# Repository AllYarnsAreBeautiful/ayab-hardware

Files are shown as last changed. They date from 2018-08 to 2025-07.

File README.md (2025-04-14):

# AYAB Hardware
This is the respository for the open-source first-party hardware that interfaces with the AYAB desktop software. It contains design files, production files, and assembly documentation, sorted by hardware generation.

The AYAB project started with the original AYAB Shield, which mounts to an Arduino Uno. The shield does not fit inside the machine and it must remain open while installed. These are often sold in kits and require assembly by the user.\
This design was later incorporated into a replacement PCB to be installed into the knitting machine, called the AYAB-Interface, and was designed and produced by Evil Mad Scientist Labs (EMSL).\
In anticipation of the new generation of AYAB software with the launch of v1.0, we have also started design on a new generation of hardware with a custom, fully integrated ESP32 microcontroller. AYAB-ESP32 supports KH 270, 900, 910, 930, 940, 950, 965, and CK-35, which would replace the internal motherboard of the knitting machine (in an easily reversible way) and allow for wireless pattern upload and operation from various mobile devices.

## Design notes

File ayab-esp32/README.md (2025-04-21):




# AYAB-ESP32
These are the design files for the latest generation of AYAB hardware, a new, next controller for knitting machines.\
It currently has compatibility with the Brother KH 900, 910, 930, 940, 950, 965, with support planned for CK-35 and KH-270.\
Based on the ESP32, many new features have been implemented:\

* Supports all carriages (K, L, and G)
* Can be powered from internal Brother power supply, or 9-12V DC barrel jack of any polarity.
* PC connection via USB-C, with future web-app planned for "wireless" use.
* Qwiic I2C connector available for user expansion or accessories (color changer, motorized carriage, etc)
* 8 User-accessible GPIO brought out on 2.54mm headers.
* 1 User-programmable button.
* Hackable - access to the solenoid control bus from outside devices for direct control of the machine.
* Friendly design for assembly. Single-sided PCB with minimum package size of 0603 and optimized BOM.
* OSHW certified design!

The project was designed using KiCad 8. All symbols, footprints, and models are self contained to this repository so no additional files are required in order to view or modify the design.

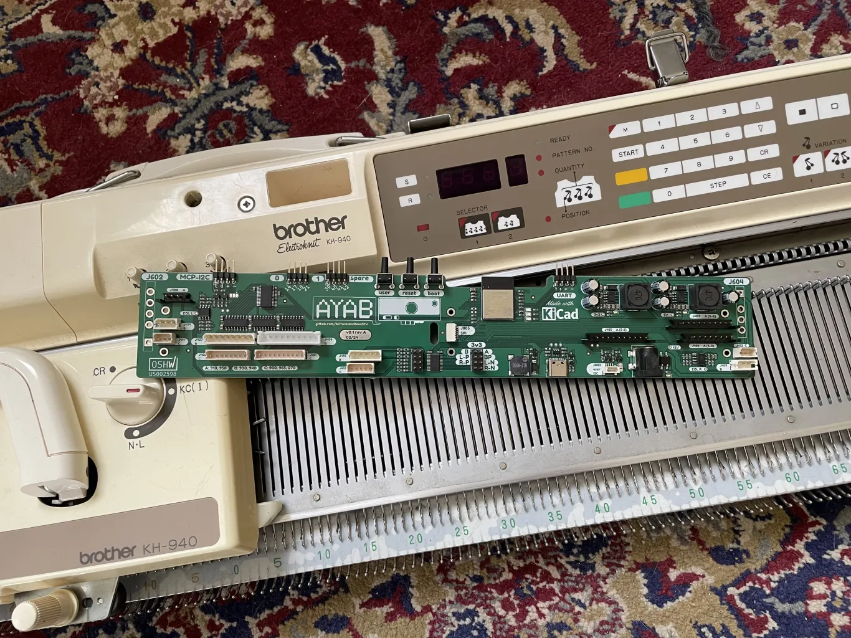
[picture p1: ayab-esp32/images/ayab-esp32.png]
Prototype hardware assembly

Live Render

Questions? Comments? Great ideas? Talk with us in [#hardware-development on Discord](https://discord.gg/A8KE3jcCn2)!

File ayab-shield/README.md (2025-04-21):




# AYAB Shield
This is the original design for the AYAB hardware. It is a board in a shield form factor intended to be used with Arduino Uno type development boards. It should be compatible with Uno R2, R3, and R4. 
This shield can be built in a variety of configurations that allow for compatibility with Brother KH 270, 900, 910, 930, 940, 950, 965.

The files required to order/build the board can be found in the Releases on the sidebar, but you can also find workflow artifacts for unvalidated hardware based on the state of the repo.

The project was designed using KiCad 9. All symbols, footprints, and 3D models are self-contained to the repository.

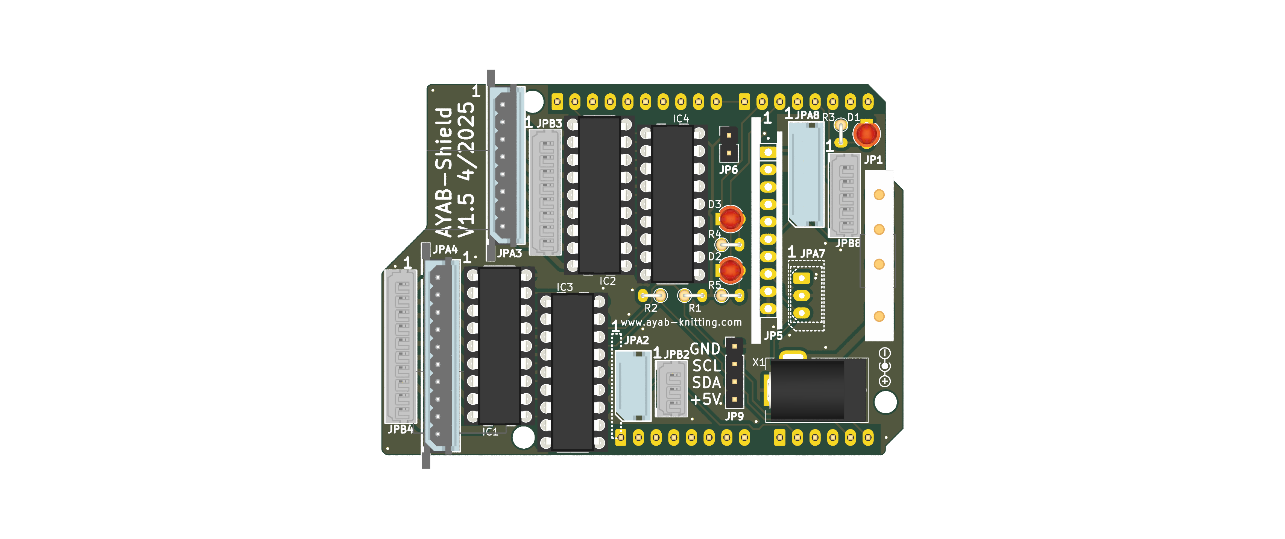
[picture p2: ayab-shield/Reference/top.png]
Live Render


Questions? Comments? Great ideas? Talk with us in [#hardware-development on Discord](https://discord.gg/A8KE3jcCn2)!

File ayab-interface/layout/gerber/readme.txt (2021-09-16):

AYAB-EMS Interface Board - Rev F
Designed by Evil Mad Scientist Laboratories
in cooperation with ayab-knitting.com

An open source hardware+software project. :)

This directory contains the following files:
 
ayab_rs.top.gbr	   			- Top copper artwork
ayab_rs.topmask.gbr 			- Top soldermask
ayab_rs.topsilk.gbr			- Top Silkscreen 

ayab_rs.bottom.gbr	 		- bottom copper artwork
ayab_rs.bottommask.gbr		  	- bottom soldermask
ayab_rs.bottomsilk.gbr			- Bottom Silkscreen

ayab_rs.plated-drill.cnc      		- NC drill file (For plated holes)
ayab_rs.unplated-drill.cnc    		- NC drill file (for unplated holes)

ayab_rs.DrillDrawing.gbr   	 	- drill Drawing with outline 
ayab_rs.outline.gbr			- Outline drawing

ayab_rs.toppaste.gbr    	 	- Solder paste file (top)

The PCB specifications are as follows:

All specifications given in INCHES or MILS.
Board size (max): 11.000 x 1.900 INCHES   (279.4 mm x 48.3 mm) 
Material: FR4
Thickness: 0.062" (1.6 mm) nominal
Layers: 2
Copper weight: 1 oz.

Individual routing according to outline on ayab_rs.outline.gbr layer.

Min Trace/Space: 8 mil
Min. Annular Ring: 12 mil

The following additional specifications are default for this board:

Finish: Pb-Free HASL, RoHS Compliant
Soldermask: BLACK LPI, both sides
Silkscreen Legend: WHITE, both sides.

UL Compliant with mark.  Add UL mark to BOTTOM SILKSCREEN.

NO FACTORY MARKS ALLOWED ON TOP SIDE OF PCB
FACTORY MARKINGS MAY BE APPLIED TO BOTTOM SIDE OF PCB (IN SILK) IF NECESSARY.

RoHS Compliant fabrication
Full electrical test of printed circuit boards is required.

NO CHANGE to any copper without prior approval.

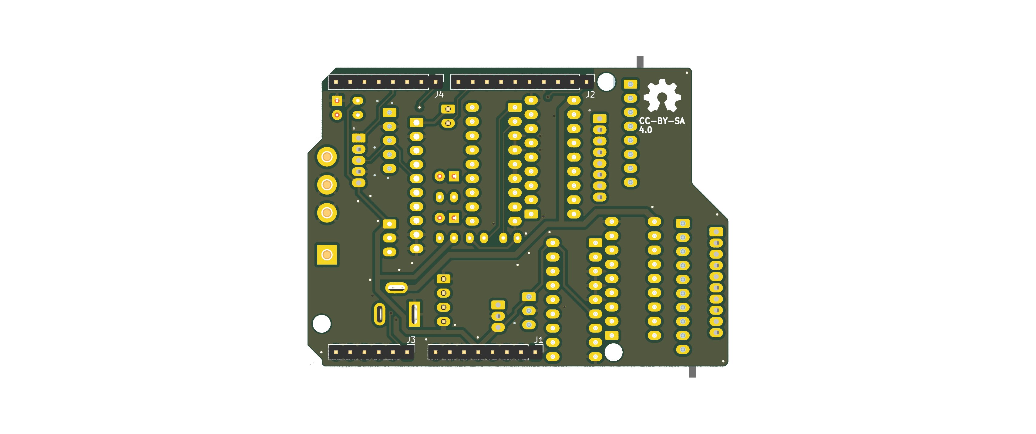
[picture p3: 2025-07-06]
ayab-shield/Reference/bottom.png

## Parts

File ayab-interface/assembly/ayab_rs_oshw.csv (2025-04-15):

Line | QTY | Reference | Type | Value | Footprint | Pin Count | Side | Manf | Manf PN | Alt. Manf | Alt Manf PN | DIGI-KEY # | Mouser # | Fabrication note
1 | 1 | - | PCB | AYAB-EMS-1 Circuit Board |  |  |  |  | 60-0043/E
2 | 1 | U1 | Microcontroller | Adafruit Metro Mini |  | 28 | BOT | Adafruit | 2590 |  |  | 1528-1374-ND | 485-2590 | DO NOT POPULATE. Mask holes if wave soldered
3 | 2 | U1 | Header | Header, 0.1", 14-pin, male-male short | PTH | 14 | BOT | 4UCon | 17168
4 | 1 | S1 | Switch | Tactile button switch | SMT Switch | 4 | TOP | TE Connectivity | FSM4JSMATR |  |  | 450-1129-ND | 506-FSM4JSMATR
5 | 1 | L1 | Buzzer | BUZZER MAGN 5V 2.4KHZ PCB | PTH | 2 | TOP | PUI | AT-1224-TWT-5V-2-R | Soberton | WT-1205 | 668-1470-ND | 665-AT1224TWT5V2R
6 | 4 | C1,C4,C5,C6 | Capacitor | 1 uF Ceramic 1206 | 1206 | 2 | TOP | Kemet | C1206C105M3RACTU |  |  | 399-8148-1-ND | 80-C1206C105M3R
7 | 1 | C2 | Capacitor | 0.1 uF Ceramic 0603 | 603 | 2 | TOP | Kemet | C0603C104K3RACTU |  |  | C0603C104K3RACTU | 80-C0603C104K3R
8 | 1 | C3 | Capacitor | 22 uF 20 V tantalum, Case B | SMT Cap. | 2 | TOP | AVX | AVX_TAJB226K020RNJ | AVX | AVX_TAJB226M020RNJ | 478-1683-1-ND | 581-TAJB226K020R
9 | 1 | D1 | Diode | DIODE SCHOTTKY 40V 2A | DO214AA | 2 | TOP | Micro Commercial | SK24-TP |  |  | SK24-TPCT-ND | 833-SK24-TP
10 | 4 | D2, D3, D5, D6 | LED | SMT RA, blue, 90 mCd min. | 805 | 2 | TOP | Lite-On | LTST-S220TBKT | Kingbright | APA2106QBC/D | 160-2032-1-ND | 859-LTST-S220TBKT
11 | 3 | R1, R7, R8 | Resistor | 5k, 5%, 1/8 W | 805 | 2 | TOP | Stackpole | RNCP0805FTD4K99 | Bourns | CR0805-FX-4991ELF | RNCP0805FTD4K99CT-ND | 652-CR0805FX-4991ELF
12 | 4 | R2, R4, R5, R6 | Resistor | 62, 1/4W or higher | 805 | 2 | TOP | Rohm | ESR10EZPJ620 |  |  | RHM62KCT-ND | 755-ESR10EZPJ620
13 | 1 | R3 | Resistor | 330, 5%, 1/4W | 805 | 2 | TOP | Rohm | ESR10EZPJ331 |  |  | ESR10EZPJ331 | 755-ESR10EZPJ331
14 | 4 | RN1,RN2,RN3,RN4 | Resistor array | 1k, 5%, 4 X Isolated array | 1206 | 8 | TOP | Yageo | YC164-JR-071KL | Bourns | CAT16-102J4GLF | YC164J-1.0KCT-ND | 652-CAT16-102J4GLF
15 | 1 | Q1 | Transistor | NPN 40V 0.2A | SOT-23-3 | 2 | TOP | ON Semi | MMBT3904LT1G |  |  | MMBT3904LT1GOSCT-ND | 863-MMBT3904LT1G
16 | 2 | U2,U3 | IC | PCF8574, I2C IO Expander | 16-SOIC | 16 | TOP | TI | PCF8574DWR | NXP | PCF8574T/3,512 | 296-13108-1-ND | 595-PCF8574DWR
17 | 2 | U4, U5 | IC | ULN2803A, Transistor array | SO-18W | 18 | TOP | TI | ULN2803ADWR | Toshiba | ULN2803AFWG | 296-15777-1-ND | 595-ULN2803ADWR
18 | 1 | J5 | Jack | Power Jack, 2.1x5.1 mm, rated for 2A DC | PTH | 3 | BOT | CUI | CP-002AH-ND | CUI | PJ-002AH | CP-002AH-ND | 490-PJ-002AH | Bottom side of PCB
19 | 2 | J2B, J6B | Molex Jack (2.5mm) | Molex 5267 Series, 3 position Male | PTH | 3 | TOP | Molex | 99-99-0987 | 4UCON | 1678 | WM2889-ND | 538-99-99-0987 | Orientation of connectors is critical
20 | 1 | J3B | Molex Jack (2.5mm) | Molex 5267 Series, 5 position Male | PTH | 5 | TOP | Molex | 99-99-0989 | 4UCON | 1680 | WM2891-ND | 538-99-99-0989 | Orientation of connectors is critical
21 | 1 | J4B | Molex Jack (2.5mm) | Molex 5267 Series, 8 position Male | PTH | 8 | TOP | Molex | 99-99-0992 | 4UCON | 1683 | 0099990992-ND | 538-99-99-0992 | Orientation of connectors is critical
22 | 1 | J5B | Molex Jack (2.5mm) | Molex 5267 Series, 10 position Male | PTH | 10 | TOP | Molex | 99-99-0994 | 4UCON | 1685 | 0099990994-Nd | 538-99-99-0994 | Orientation of connectors is critical
23 | 2 | J2C,J6C | Molex Jack (2mm) | Molex 53014 series, 3 position male | PTH | 3 | TOP | Molex | 53014-0310 | Molex | 53253-0870 | WM18967-ND | 538-53253-0870 | Orientation of connectors is critical
24 | 1 | J3C | Molex Jack (2mm) | Molex 53014 series, 5 position male | PTH | 5 | TOP | Molex | 53014-0510 | Molex | 53253-1070 | WM18968-ND | 538-53253-1070 | DO NOT POPULATE. Mask holes if wave soldered
25 | 1 | J4C | Molex Jack (2mm) | Molex 53014 series, 8 position male | PTH | 8 | TOP | Molex | 53014-0810 | Molex | 53253-0370 | WM18971-ND | 538-53253-0370 | DO NOT POPULATE. Mask holes if wave soldered
26 | 1 | J5C | Molex Jack (2mm) | Molex 53014 series, 10 position male | PTH | 10 | TOP | Molex | 53014-1010 | Molex | 53253-0570 | WM18973-ND | 538-53253-0570 | DO NOT POPULATE. Mask holes if wave soldered
27 | 1 | J7A | Latching Header (2.5mm) | Hirose HNC series, 3 position male | PTH | 3 | TOP | Hirose | HNC2-2.5P-3DS(02) |  |  | HNC2-2.5P-3DS(02)-ND | 798-HNC2-2.5P-3DS02 | Orientation of connectors is critical
28 | 1 | J3A | Latching Header (2.5mm) | Hirose HNC series, 8 position male | PTH | 8 | TOP | Hirose | HNC2-2.5P-8DS(02) |  |  | H124015-ND | 798-HNC2-2.5P-8DS02 | Orientation of connectors is critical
29 | 2 | J2A,J5A | Latching Header (2.5mm) | Hirose HNC series, 10 position male | PTH | 10 | TOP | Hirose | HNC2-2.5P-10DS(02) |  |  | HNC2-2.5P-10DS(02)-ND | 798-HNC22.5P10DS02 | Orientation of connectors is critical
30 | 2 | J8, J9 | Header | 4-pin PTH Male Pin, 2.54 mm pitch | PTH | 4 | TOP |  |  |  |  |  |  | DO NOT POPULATE. Mask holes if wave soldered

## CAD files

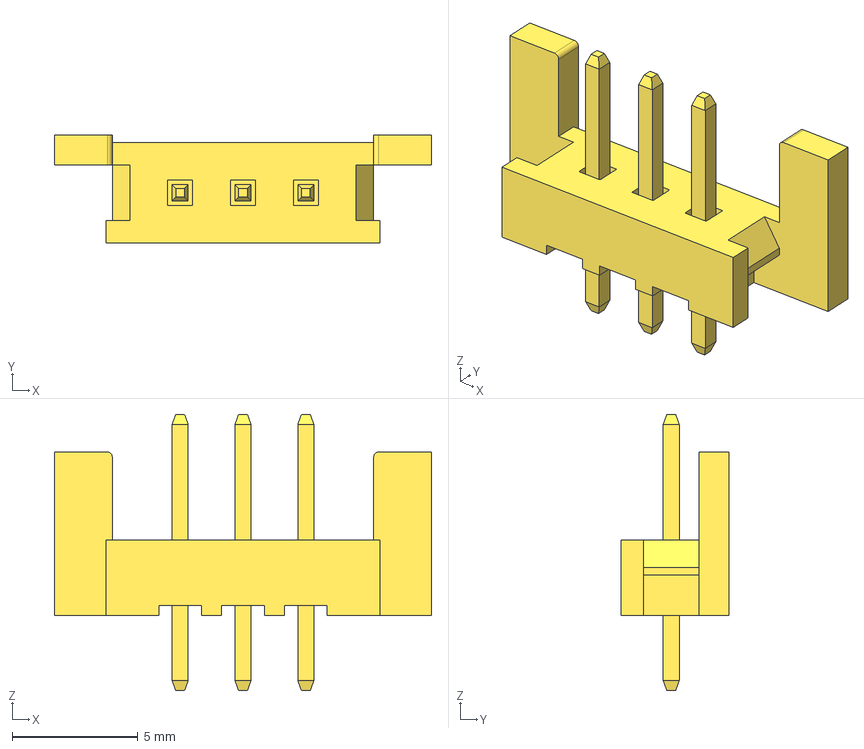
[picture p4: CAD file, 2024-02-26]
ayab-esp32/freecad/910_950_HRS_Connectors.FCStd
15.0 x 4.30 x 11.0 mm

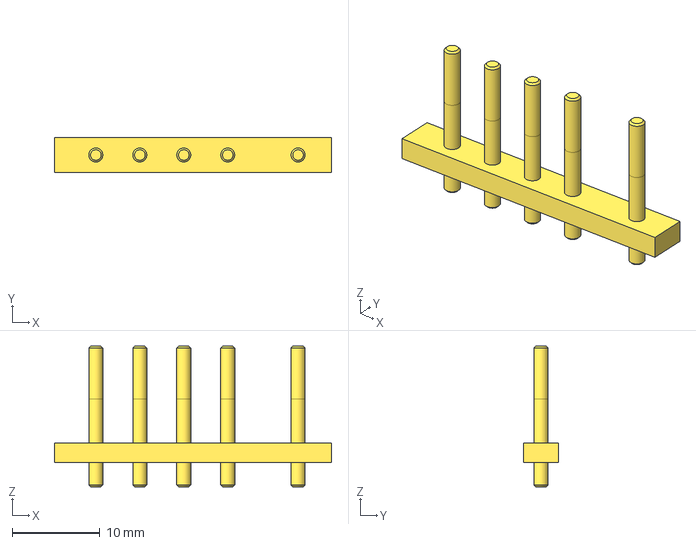
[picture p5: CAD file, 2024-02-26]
ayab-esp32/freecad/Brother_5P.FCStd
31.5 x 4.00 x 16.0 mm

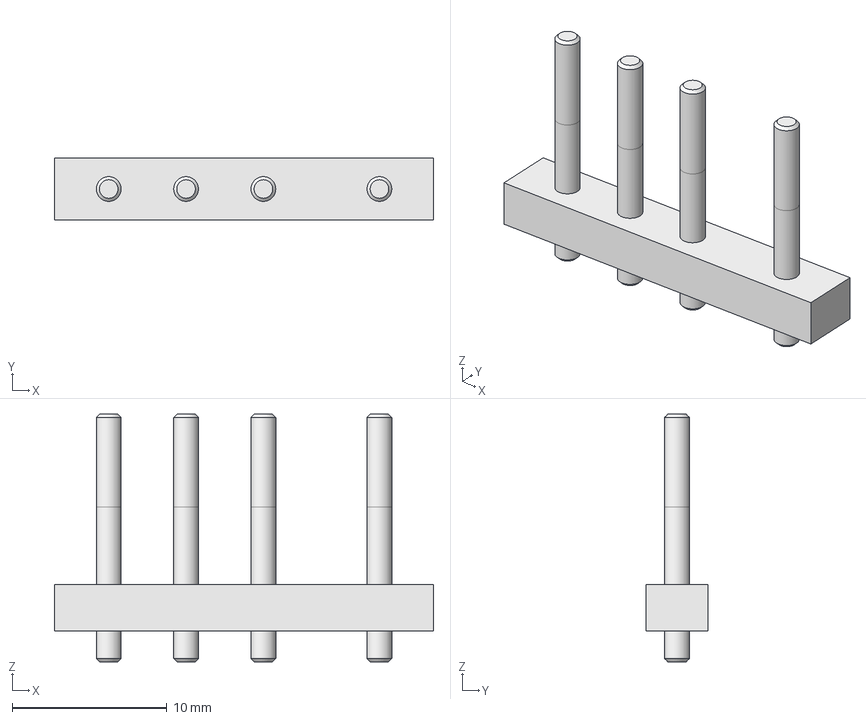
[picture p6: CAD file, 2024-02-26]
ayab-esp32/freecad/Brother_4P.FCStd
24.5 x 4.00 x 16.0 mm

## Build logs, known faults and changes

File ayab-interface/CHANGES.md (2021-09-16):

# AYAB Shield v2 Release Changes

## Version F

- Fiducial marks removed from top of PCB
- Two holes removed
- Assembly tab removed
- Secret message removed
- EMS catalog number removed and Woolly Logic PCB code substituted
- OSHW logo added
- Woolly Logic logo added
- SMD Tantalum capacitor substituted for SMD electrolytic capacitor C3
- Woolly Logic PCB code KI01

## Version E

Evil Mad Science catalog number EMS 60-0043/E

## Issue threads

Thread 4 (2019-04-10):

License missing?

DerAndere1, 2019-04-10:
With the AYAB software being GPL3.0, would'nt it make sense to also add a license to the ayab-hardware repository? It could become licensed under the terms of the GPL 3.0 like Arduino hardware or you could choose something more permissive which works well for hardware (e.g. Creative Commons Attribution 4.0 International License, [CC BY 4.0](https://creativecommons.org/licenses/by/4.0/legalcode) ? Currently you as copyright holders have all rights reserved (https://help.github.com/en/articles/licensing-a-repository ) so the content of this repository cannot be used by anyone without your explicit permission.

chris007de, 2019-04-11:
Back then, we intended to use CC-BY-SA 4.0 for the AYAB Shield, and I thought that we had documented this somewhere (but obviously this is not the case, as I struggle to find the place).
But I hesitate to just add the license for the whole repository now, as it also contains the data for the EMSL AYAB Interface (folder Shieldv2x).
So either we agree on a common license for both pieces of hardware or we have to split into two repositories.
@oskay what are your thoughts on this? Which license did you intend for the EMSL interface?

oskay, 2019-04-11:
The EMSL AYAB interface boards are CC-BY-SA 4.0, which I used since I believed that was the chosen license for the AYAB project. However, it is my copyright to assign, so I'm happy to license it under other terms (in addition or instead of those) if you prefer. You have my full permission to set the license type, as you see fit, for that set of hardware designs.

Also, GPL is a kind-of iffy license structure for hardware. The TAPR OHL or CERN OHL may be better models to start with.

chris007de, 2019-04-14:
We'll stick to the CC-BY-SA 4.0 license for now.

Closed 2019-04-14.

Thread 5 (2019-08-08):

Shield V2 Footprints U2 and U3 in Gerber files do not match SSOP20

atrophy, 2019-08-08:
The footprints on the current version of the Gerber files don't match the SSOP20 part listed in the BOM. Should we be using the SOIC version of the PCF8574?

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

oskay, 2019-08-08:
Yes, looks like that's an error on the BOM.

oskay, 2019-08-08:
Are you fabricating boards to sell?

atrophy, 2019-08-08:
Not to sell no, I work at Fab Lab Wgtn, part of Massey University and we're converting a couple of the university's knitting machines over to use in the lab.

oskay, 2019-08-09:
(That's fine -- we're still hoping to find someone happy to make and sell a batch.)

chris007de, 2019-08-11:
Thanks a lot for fixing this issue!

Closed 2019-08-11.

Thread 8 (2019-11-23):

Feature suggestions for AYAB interface

t0mpr1c3, 2019-11-23:
Eventually I would like to re-design the AYAB interface. Some improvements that I could suggest are straightforward (e.g. longer USB cable). Others incremental (e.g. migrating from Adafruit Mini Metro to something cheaper, 1x MCP28017 instead of 2x PCF8574, common bus resistor networks). In my view the most important area for new development is revamping the enclosure. But I will need to play around a good deal before coming to any conclusions on that.

Does anybody have any thoughts or feelings that they would like to chip in?

chris007de, 2019-11-23:
@oskay @andz82

oskay, 2019-11-24:
We have made some prototype enclosures, that worked pretty well, but weren't able to go to the next stage with that.  @t0mpr1c3 we can chat about that offline.

There's not much issue with changing to a lower-cost USB/micro interface, but take care that it does not accidentally increase the cost instead.

I would be *very* careful about going to a different I/O expander. The AYAB software has to support every version of the AYAB hardware, and adding *yet another* chipset to support should only be done if there is a **clear and compelling reason**.

t0mpr1c3, 2019-11-24:
Fair point about the I/O expander. Happy to chat offline about enclosures.

An attractive suggestion mentioned to me today was to reserve a pin on the microcontroller for a row-counting Hall effect sensor.

t0mpr1c3, 2021-08-03:
- Comparators are going to be faster than ADC for evaluating the Hall sensor output.
- Eventually, it will become desirable to support USB-C. I would not be surprised if Apple are planning to phase out USB-A on their laptops. USB-C is already standard on iPads and phones, which we may want to support some day.
- A chip with more IO pins would not require I2C expanders.

chris007de, 2021-08-07:
Hi Tom,

> * Comparators are going to be faster than ADC for evaluating the Hall sensor output.

We have to keep in mind that there obviously are different hall values for different machine types, therefore these comparators would have to be compatible to either levels (https://github.com/AllYarnsAreBeautiful/ayab-firmware/blob/master/settings.h#L49)

> * Eventually, it will become desirable to support USB-C. I would not be surprised if Apple are planning to phase out USB-A on their laptops. USB-C is already standard on iPads and phones, which we may want to support some day.

Good point...it may be worth to check. I like the USB-C port as well for it's rigidness.
Still, if a host device currently has USB-C, there is still the possibility to use a USB-C to Micro-USB cable for now. USB-C <-> USB-C cables are still pretty rare in the wild (at least in my bubble of colleagues, family and friends).

> * A chip with more IO pins would not require I2C expanders.

Guess that's probably a decision of costs...bigger chip might cost more than I2C expanders.

oskay, 2021-08-07:
USB C support is trivial; that's just a cable type, and it's straightforward enough to switch to a USB C cable. The real concern is that future devices may, at some point, not support USB 2.0. Thus far, newer versions of USB (including properly built USB 3 cables) do generally support USB 2.0 for backwards compatibility.

t0mpr1c3, 2021-08-07:
> We have to keep in mind that there obviously are different hall values for different machine types, therefore these comparators would have to be compatible to either levels (https://github.com/AllYarnsAreBeautiful/ayab-firmware/blob/master/settings.h#L49)

Yes, a disadvantage is that you would need one comparator (and hence one pin) per level. The data acquisition would be basically instantaneous, whereas reading the ADC takes about 0.1ms. Although I suspect UART communication between the Atmega and its USB bridge is the major bottleneck in terms of response time.

t0mpr1c3, 2021-08-07:
> USB C support is trivial; that's just a cable type, and it's straightforward enough to switch to a USB C cable. The real concern is that future devices may, at some point, not support USB 2.0. Thus far, newer versions of USB (including properly built USB 3 cables) do generally support USB 2.0 for backwards compatibility.

This is good to hear. I hate micro USB, the cables are flimsy and always breaking. A real downgrade from mini USB.

oskay, 2021-08-07:
The micro connectors are designed to last for twice as many cycles as mini:
https://en.wikipedia.org/wiki/USB_hardware#Durability

t0mpr1c3, 2021-08-09:
It's not the connection that fails, it's the cable itself.

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

Rixstaa, 2023-02-20:
I would like to have a option to use a different motor to make all carriages electronic with some switch on each end for it to go left to right with out doing it manualy. Would also like to know if theres a different hall position sensors we can use as originals are becoming hard to find, maybe schematic to make some etc or already a arduino one that will work? I was even thinking adding a tft screen would be nice for some check functions.

t0mpr1c3, 2023-02-20:
There isn't anything complicated about the Hall sensors as far as I can
remember. Remanufacturing them would be mostly just trial and error to get
the sensitivity right.

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

Closed 2024-02-28.

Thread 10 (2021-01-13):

beeper circuit

t0mpr1c3, 2021-01-13:
The specified beeper has a coil resistance of 47 Ohms and draws 40 mA (max) through the collector of a MMBT3904 transistor and is connected to the 5 V rail through a 62 Ohm resistor.

Ignoring for the moment the Vce of the transistor and the coil inductance, that means the voltage drop across the resistor should be about 3 V and the voltage drop across the beeper is about 2 V. That's lower than its supported range of input voltages (3-7). For what it's worth, I have tried both the specified part and some cheap alternatives and they have all worked.

I haven't played around with any alternative circuits but I believe the typical application would include a flyback diode to protect the transistor. Again, I haven't noticed any problems so far.

Any thoughts?

oskay, 2021-01-13:
The most important thing is to match the beeping frequency to the device resonant frequency, to get enough loudness. Different people have different opinions about how loud a beeper should be.

t0mpr1c3, 2021-01-13:
I think I will experiment a little bit. I tend to think louder is better, as there will be a silent option in the software going forward.

oskay, 2021-01-13:
Possible option to consider for the future: Migrate to making noises in the software, not the hardware. Computers have headphone ports and things; can be made really loud or quiet, easily.

t0mpr1c3, 2021-01-13:
Yes, that will be implemented in the software in future and will make the beeper redundant. I really don't think there is any advantage to having both. Can you think of any reason to retain the beeper?

Apart from anything else, some users may have strong preferences on the subject of electronic noises and I tend to think these are more easily addressed in software.

oskay, 2021-01-13:
This is probably a question that should be brought to the userbase as a whole.

t0mpr1c3, 2021-01-14:
Yes. There will be user input to the software update and that should clarify things.

VIPQualityPost, 2024-02-27:
https://github.com/AllYarnsAreBeautiful/ayab-firmware/pull/143
beeper configuration implemented, seems issue is closed

Closed 2024-02-27.

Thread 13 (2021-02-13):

Output impedance of Hall sensors

t0mpr1c3, 2021-02-13:
Has anyone measured it? I imagine it is buffered by a LM358.

VIPQualityPost, 2024-02-27:
Was there a concern associated with this?
New design is hi-z / buffered anyway so no issue with loading for the new boards at least.

t0mpr1c3, 2024-02-27:
I think my original concern might have been that the output from the Hall sensor might be a floating collector from a comparator, in which case you would need a pull up.

Closed 2024-02-28.

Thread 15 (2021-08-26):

Migration from Metro Mini

t0mpr1c3, 2021-08-26:
Eventually I would like to move to a v3 interface that does not rely on the Metro Mini. At some point in the future Adafruit will retire it, and there is no replacement board with the same form factor.

The closest like-for-like replacement would be the Arduino Nano Every.
- Open source.
- Functionally equivalent.
- Nano form factor is almost the same size.
- Similar price.

The Every even offers a couple of small improvements.
- More flash, more RAM.
- Castellated and no components on the back, so it can be soldered directly to the PCB.

Nevertheless, I am also looking at the possibility of putting a microcontroller directly on the interface.
- Must have: Arduino-compatible IDE, run at 5V.
- Strong preference: fast Arm M0 or M0+ with at least as much flash and RAM as the Every.
- Nice to have: enough IO pins that expanders are no longer necessary, hardware support for USB 2.x.

AFAIK the only chip that meets all these criteria is the NUC123LD4AN0 as used on the DFRduino M0 (SKU: DFR0392). I'm playing around with a DFRduino M0 at the moment to get an idea of how much work it would take to retool the firmware.

t0mpr1c3, 2021-09-01:
Files for Nano prototype are here: https://github.com/t0mpr1c3/ayab-hardware/tree/nano/Shieldv2x

although I should probably move them to a new folder Shieldv3x. I'll have some PCBs made in the next couple of weeks.

cb88, 2021-12-02:
> Files for Nano prototype are here: https://github.com/t0mpr1c3/ayab-hardware/tree/nano/Shieldv2x
>
> although I should probably move them to a new folder Shieldv3x. I'll have some PCBs made in the next couple of weeks.

What's the status of the Nano Every prototype? I picked up a KH-910 and am planning on getting it going for Christmas for my mother and sisters ;-) ... I'm contemplating which interface board to order (probably from JLCPCB) since I like it better than the shield.

One alternative you might consider is the PSOC5  and you probably wouldn't need IO expansion then. https://www.sparkfun.com/products/13714

RISCV could be possible also the Longan Nano is 3.3v but most of the pins are 5V tolerant... even if they can't directly drive 5V. that board also has rust support if you wanted to tickle that itch.

I have a fondness for PIC32/Chipkit but it clearly doesn't meet your IO requirements at all...

USB port type really doesn't matter that much IMO and USB 2.0 is gonna be supported virtually forever, its not a big deal to interface to original low speed devices even now from a USB 3.1 gen 2 port etc... on most devices worst case you can always go through a hub anyway.

t0mpr1c3, 2021-12-02:
I've built a prototype but I haven't made any attempt to migrate the code
base.

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

VIPQualityPost, 2023-05-01:
hi,
I recently started working on developing my own replacement mainboard for these machines, only to recently find your project. My board is designed for low-cost assembly and based on the STM32F103, using USB C for connection to PC and an on-board power supply.  AYAB seems really interesting and I am more of a hardware guy than software and it seems you have done a lot of legwork here on that front- I am happy to lend a hand with any hardware design, schematic review, etc. I would love to help out. Also, the link to join your discord does not work.

t0mpr1c3, 2023-05-01:
Try this link: https://discord.gg/Gpwakzys

I think that currently, the consensus long term goal is to migrate the desktop software to a webapp and the hardware to ESP32.

The short term consensus is to stick with Adafruit mini metro, although personally if I ever get around to manufacturing the boards again I will be looking to switch to the Arduino Every which is more or less a drop in replacement.

VIPQualityPost, 2024-02-27:
Closing as new hardware is, indeed, ESP32 based.

Closed 2024-02-27.

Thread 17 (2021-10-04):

Machine selection

t0mpr1c3, 2021-10-04:
For v1.0, the plan is to select the machine from a drop-down menu instead of it being hard-coded in the firmware.

Another solution would be to have machine type hard coded on the shield. The obvious way to do this would be to connect a resistor divider to an analog pin. If the shield is intended to be used with more than one type of machine, this could be done using a DIP switch and resistor ladder.

When the desktop software starts up, it can check the voltage on the pin to determine the machine type. If no resistor is connected, software selection can proceed.

chris007de, 2021-10-05:
Do I understand correctly that you propose this to be an additional (/optional) way for automatic machine type identification?
So if the software does not recognize a machine type automatically, it falls back to manual selection in software?

From my experiences, having as few possible points of failure/misconfiguration is desirable. By having software selection only, it is pretty obvious where to set things up. When having a hardware switch (reconfigurable DIP switch without need to solder would be a must-have in my opinion), things already get a bit more complicated, as somebody has to check things on the AYAB interface as well if somethings goes wrong.

t0mpr1c3, 2021-10-05:
I understand your concern about making things more complex than they need to be. I just sort of improvised the DIP switch idea, thinking that people might want boards that can be used with multiple different machines. Maybe that is a bad idea, and just staying with software selection makes more sense in this case.

For people with existing boards, nothing would change: selection would be done in software.

For new boards, machine type would be automatically detected, and the machine type options in the preferences dialog would be greyed out. It actually makes things simpler for users, who would no longer be able to select the wrong machine in the preferences.

The hardware changes are minimal. v2 shields are already machine-specific: they have different covers and connectors depending on machine type. This change would just involve a couple of extra resistors attached to one pin. If software selection is preferred (perhaps because the user possesses adapter cables that can connect the shield to another type of machine), then these resistors can simply be omitted from the circuit board, enabling software selection of the machine type.

VIPQualityPost, 2024-02-27:
It seems like we didn't address this in the new design, but also having it assembled by third party makes it annoying to tinker with the BOM for each potential machine/customer.

This does remind me we should revisit the OTP/ hardware revision programming soon though, certainly before we push the ESP32 design out of prototype.

t0mpr1c3, 2024-02-27:
Setting the machine in software seems good enough for now, I agree with Chris that a jumper is probably all we need to set it in hardware if we want to go that route.

VIPQualityPost, 2024-02-28:
OK, on the current rev of ayab-esp32, we only have 3 unused pins, these could be used for hardware ID (8 possible machines) but imo this is not super necessary and makes it difficult/impossible to use those pins later if we need to change things down the line. I would suggest that we just stick with sw machine identification for now.

t0mpr1c3, 2024-02-29:
Currently we have 3 hardware types and we can define that using one pin and one jumper.
0 = no jumper
1 = jumper between pin and ground
2 = jumper between pin and 3V

So we could break out one spare pin plus ground and 3V to a 3 pin header and have 2 spare pins for other stuff.

VIPQualityPost, 2024-02-29:
Oh, I totally misunderstood this as Brother machine identification, not AYAB hardware... There are already firmware defines to the new platform, we can just add something there and also have it return something in the identification step of the communication with some hex ID.

VIPQualityPost, 2024-02-29:
Unless you thnk the next generation AYAB hardware will also be build on ESP32-S3 this seems like the best way to handle it I think.

t0mpr1c3, 2024-02-29:
Yes. So do we agree that we'll do the machine selection in software, and the board will have some kind of identity defined in firmware?

VIPQualityPost, 2024-02-29:
Yes, I agree.

t0mpr1c3, 2024-03-01:
Closing as nothing is required for hardware.

Closed 2024-03-01.

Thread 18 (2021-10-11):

What software is used for schematic ?

OddmarDam, 2021-10-11:
Hi.

What software is used for this schematic ? Is it Eagle or Kicad or something else ?

chris007de, 2021-10-12:
> http://www.geda-project.org/

That's for Shieldv2x ("AYAB Interface"). For Shieldv1x ("AYAB Shield") it's eagle.

> Unfortunately this software is no longer actively maintained. I use the Ubuntu 16.04 version.

For this reason, I'd propose to move to KiCAD sooner or later, as it's actively developed FOSS.

t0mpr1c3, 2021-10-12:
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

I agree. I hear good things, I just haven't got around to learning how to use it.

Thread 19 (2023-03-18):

Correct right hall sensor detection

dl1com, 2023-03-18:
see https://github.com/AllYarnsAreBeautiful/ayab-firmware/issues/51#issuecomment-1467086056 and following

VIPQualityPost, 2023-07-17:
So what is the resolution to this?
Do we want to have two input pins for 910 EOL, one for K and one for L?
Or should we just OR the two signals, because we can sense if the carriage has moved >3 needles but shows a pulse longer than single magnet?

maybe we can get some comments from @jpcornil-git

jpcornil-git, 2023-07-17:
I would use both (digital) inputs to avoid another (less robust ?) detection mechanism for LKG carriages.

One input is indeed equivalent to "hallValue < FILTER_R_MIN" and the other to "hallValue > FILTER_R_MAX" and existing code can therefore easily be modified to cope with this.

jpcornil-git, 2023-07-17:
I would use both (digital) inputs to avoid another (less robust ?) detection mechanism for LKG carriages.

One input is indeed equivalent to "hallValue < FILTER_R_MIN" and the other to "hallValue > FILTER_R_MAX" and existing code can therefore easily be modified to cope with this.

jpcornil-git, 2023-07-17:
... and you can't differentiate K and L anymore with an OR approach (one short pulse for both) -> not an option anyway

VIPQualityPost, 2023-07-17:
Right, I was thinking because they are a pulse that you can do it, but it doesn't work for other machines anyway. It will have it's own pin.

VIPQualityPost, 2024-02-27:
We did it!

Closed 2024-02-27.

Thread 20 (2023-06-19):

[WIP] Requirements for Next-Gen Hardware

dl1com, 2023-06-19:
# Introduction

As discussed in the developer meetings and on Discord, we want to go for a new AYAB hardware more sooner than later.
Here is a collection of requirements. This serves as a common ground for discussion in Discord and developer meetings.
Once all (or at least the most significant) topics are consolidated, this issues serves as meta issue and the requirements are split into separate issues/tasks.

Many of this is work in progress and to be discussed (marked with a ❓). Once it seems that there is a common opinion for a topic, the ❓ will be removed.
Design decisions to be made are marked with a ⚖️.
This first post will get updated continuously to reflect the current state of discussion.

# Requirements and Design Decisions

## Form factor / Dimensions

- The board shall have the same dimensions as the EMSL AYAB Interface to be able to be fitted into the machine
- The components and connectors shall be placed as similar as possible as on the EMSL AYAB Interface to ensure its compatibility to the cable lengths and the space in the machine.

## High level

- The board shall enable the usage of the current AYAB APIv6 over a USB Serial connection
- The board shall provide Wifi connectivity to enable a future shift to a wireless connection from the AYAB Desktop software
- The board shall provide enough ressources (i.e. flash memory, RAM) to be able to serve a web interface (i.e. written in a JS framework like vue.js) which reflects the functionality of AYAB Desktop v1.0

## Power Supply

- The board shall use *only* an external power supply to enable usage in machines where the original power supply is broken
- The board shall use a standard interface for power supply, a barrel connector
- The board shall have protection against wrong power supply polarity
- The board shall use USB-C for data connection
- ❓⚖️ The board shall/shall not provide an On/Off switch

## Controller

- The board shall use a microcontroller with integrated Wifi connectivity
- The board shall use an ESP32 microcontroller as it is very well supported and available. Numerous examples show that it is capable of serving web applications hosted on the controller via Wifi. (other suggestions? Pi Pico /w Wifi?)
- The controller (i.e. WROOM module) shall be soldered directly onto the board

## Components

- The board shall use "common available" components, i.e. no "exotic" parts, so the probability of missing parts/obsolenscence is reduced.
- The board shall provide the following LED indicators:
  - User faced:
    - Power LED
    - Wifi Status (RGB)
- The board shall provide the footprint for a buzzer

## Expandability

- The board shall provide a generic interface for future extensions (i.e. display), i.e. expose the I2C pins to a connector.

## Bugfixes / Lessions learned from earlier versions

- The missing sensor signal for proper carriage detection has to be connected (see https://github.com/AllYarnsAreBeautiful/ayab-hardware/issues/19)

## Software Interface

- The board has to be supported by the AYAB firmware
- The board has to be supported by the AYAB Desktop software

## Organizational decisions & Tooling

- The board shall become OSHW certified
- The board shall be designed using KiCAD 7
- The board data shall be hosted in ayab-hardware repository (new folder, better naming than current)
- The repository shall have a GitHub action for automatic generation of HTMLBom
- The repository shall have a GitHub action for automatic generation of KiDiff visual diff

# Design draft

Made by @jpcornil-git
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

t0mpr1c3, 2023-06-30:
Possible serial EEPROM e.g. 24FC type to store hardware information. (https://github.com/AllYarnsAreBeautiful/ayab-firmware/issues/106)

VIPQualityPost, 2024-02-27:
I think we hit all of these things, with the exception of generating production files (gerber, BOM, CPL).
However, with the new release of Kicad 8, there is improved kicad-cli support for generating these files, so we can probably set up CI for this.

Closed 2024-02-28.

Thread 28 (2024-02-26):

Prototype board revisions

VIPQualityPost, 2024-02-26:
- [x] fix BOM from XL1509-5.0 to XL1509-ADJ
- [x] determine why MCP I2C pullups are missing (turns out I placed two of each, somehow, and it did not make any ERC/DRC violation?
- [x] increase trace width out of 5V/3V3 regulators
- [x] User I2C port is vertical, find horizontal part and fix footprint
- [ ] 12V rail showing 4V when only plugged in via USB, determine if we need to fix this (jp identified as protection diode in XL1509)
- [x] Adjust LED resistor values to match brightness across colors
- [x] Fix silkscreen for logic-level signals on 3v3 breakout

t0mpr1c3, 2024-02-27:
Apart from the trace width from the regulators, did you notice any thermal issues? I generally just throw in lots of vias and hope for the best.

VIPQualityPost, 2025-02-10:
I think we can mark this closed since bringup is done, and instead handle the new requested changes in #38 .

Closed 2025-02-10.

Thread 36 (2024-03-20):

Current state of ayab-esp32

thoka, 2024-03-20:
We just inherited a Brother KH910 and would order some PCBs and try to build an interface for it.

Is the new interface board suitable to get it running already or would you recommend to wait for a new revision?

VIPQualityPost, 2024-06-11:
Hey! Sorry for missing your message....
I am still working on validating the new ESP32 boards, they are not quite ready for production yet. If you want to start using your machine _today_ then I would recommend that you spring for the arduino shield or the interface (long black board). However, if you are patient, I'll be done with bringup and testing in the next week or two, and after AYAB 1.0 is out, we will work on merging in support for the new hardware.

bfdkaz, 2024-12-28:
hi any progress on this. looking at buying a machine but want an interface rather than shield. thanks

VIPQualityPost, 2025-02-10:
We still didn't push out v1.0 yet, this is the reason that nobody started on firmware for this board yet, so nothing is ready still. We now launched beta5, there shouldn't be much time now until the formal release and then some work will get started again on the esp32 boards.

Maitresinh, 2025-02-19:
I've just send it to JLBpcb.... :/
It's way i could find the ESP32 script....

Closed 2025-02-10.

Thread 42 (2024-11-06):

Wrong part number for I2C port expander in AYAB interface BOM

dl1com, 2024-11-06:
In https://github.com/AllYarnsAreBeautiful/ayab-hardware/blob/main/ayab-interface/assembly/ayab_rs_oshw.csv#L17 the Manufacturer Part Number and order numbers are stating a wrong version of the chip (PCF8574A).

The correct one is PCF8574 (without trailing A).
The parts have different I2C adresses and are therefore not interchangeable, so it is crucial to fix this in order to avoid DoA interfaces.

VIPQualityPost, 2025-02-10:
Does this require any changes on the actual design in geda or can we just update the BOM file?
Is it worth maintaining interface design files? It doesn't appear you can easily import geda project to kicad, and geda seems generally poorly maintained, the last release is many years ago at this point.

VIPQualityPost, 2025-04-01:
@t0mpr1c3 Can you address above? If it's only a BOM change this is easy, otherwise I don't really care to try and modify the gEDA design...

t0mpr1c3, 2025-04-14:
>  @t0mpr1c3 Can you address above? If it's only a BOM change this is easy, otherwise I don't really care to try and modify the gEDA design...

Yes, it's just a typo in the BOM.

Closed 2025-04-18.

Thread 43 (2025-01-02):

ayab-esp32: KH910 digital right Hall sensor signals do not match what the board comparators generate

jonathanperret, 2025-01-02:
## Summary

On the `ayab-esp32` board, the KH910 digital outputs for the right Hall sensor are mixed in with outputs from the board's comparators (which are not meant to be active on a KH910). But the signals coming from the machine's built-in comparators are not compatible with those from the board's, meaning that firmware would have to interpret them differently based on the machine type.

Also, it appears that the board's comparator outputs will both sink current when the analog sensor output is left open (as would be the case on a KH910), making it impossible for the machine's digital outputs to override the board's comparator outputs.

Note that while I have measured the machine's signals on an actual KH910, the `ayab-esp32` board's behavior I posit below is only based on my understanding of the schematic and datasheets, so I apologize in advance if I made a mistake.

## Context

Here's what the comparator setup for the right Hall sensor looks like on the `ayab-esp32` board as of commit 6ace2960d:
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

If I am reading the [LM393 datasheet](https://www.ti.com/lit/ds/symlink/lm393.pdf) correctly, this should result in the following behavior for `EOL_R_K` and `EOL_R_L`:

| EOL_R | EOL_R_K | EOL_R_L |
| --- | --- | --- |
| < 0.88V  | Low | Hi-Z |
| 1.6V | Low | Low |
| > 2.94V  | Hi-Z | Low |

So far, so good when used on a machine that has an analog right Hall sensor output such as the KH930.

## KH910 situation

Because the KH910's connector for the right sensor exposes digital outputs from its built-in comparator (see https://github.com/AllYarnsAreBeautiful/ayab-hardware/issues/19), the board's comparators cannot be used.

Here is the behavior of the machine's built-in comparator outputs as measured on a KH910 (in **bold**, values that differ from the board's behavior):

| EOL_R | EOL_R_K | EOL_R_L |
| --- | --- | --- |
| < 0.88V  | **Hi-Z** | Hi-Z |
| 1.6V | **Hi-Z** | Low |
| > 2.94V  | **Low** | Low |

It appears the machine's comparator for the `K` magnet is wired in reverse of the board's, causing it to sink current only when a `K` magnet is present. As a result, firmware reading a **Low** value on `EOL_R_K` cannot determine whether a `K` magnet is present or not without taking into account the machine type.

Additionnally,  because the `EOL_R` input is left floating when connected to a KH910, it is driven to 1.6V by the biasing resistors, causing both of the board's comparators to go **Low** and sink current. This means that the machine's comparators can never cause the firmware to see anything other than the absence of a magnet.

jonathanperret, 2025-01-03:
I wanted to be sure about the 910 measurements that I did a while ago, so I redid them, with pictures so that I can be sure I didn't just write things down incorrectly.

Here's the K carriage passing in front of the right sensor, while the multimeter is monitoring pin 8 of JP5 (no pull-up resistor so the floating voltage isn't relevant, just that it's zero or not):

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

As noted above, the pin goes low only when the K carriage is detected.

Here's the L carriage, monitoring pin 7 of JP5:

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

Again, matches the table above: pin is low **unless** the L carriage is detected. This is a bit unexpected (which is why I wanted to make doubly sure my readings were correct), it feels like it would have been more logical to have each pin go low when it detects a carriage, but maybe it simplifies the implementation downstream.

jonathanperret, 2025-01-03:
@jpcornil-git confirmed on Discord that it was intended for the comparators to sink current only when the thresholds are passed, i.e. when a magnet is detected, but a misreading of the datasheet caused their inputs to be flipped.

I guess all the comparators inputs should be flipped, so that they output a low signal when they detect a magnet, and float by default, as was intended initially.

This would make the 910's pin 8 (K detector) OK to connect to the comparator output as it is already.

But the 910's pin 7 (L detector) still would need some kind of inverter to be compatible with the comparator output.

Note that you can't just flip the inputs of the L comparator (i.e. have it float when an L magnet is detected, like the 910's pin does), because this would make the comparator force the output to low when its input is floating, preventing the 910's pin 7 from overriding it.

jpcornil-git, 2025-01-04:
I would keep the comparator output high-Z when there is no detection; this makes KH910 and KH930 different for FW (minor adaptation) but allows to share the same IOs for the EOL_R signals.

I prefer to have KH910's EOL_R digital signals routed to digital inputs (with pullup enabled) and analog signals routed directly to analog pins (as of today). Note that this is what you get with the fix for JP5.7 as well (and WiFi with UnoR4).

If deemed required, you could also implement an auto-detection mechanism for KH910/930 (internal pullup on JP5.7);
- high for more than 3 needles = KH910 not connected -> switch to KH930
- low for more than 3 needes = KH910 connected -> switch KH910

For test purpose/confirm behavior, you could also connect JP7 with flying wires to arduino and connect JP5.7 to a spare GPIO (enable pullup on both JP7.7 & 8)

jonathanperret, 2025-01-04:
> Note that I prefer to have KH910's EOL_R digital signals routed to digital inputs (with pullup enabled) and analog signals routed directly to analog pins (as of today). This is what you will get with the fix of the current shield for JP5.7 as well (and WiFi with UnoR4).

I’m confused. If you want to route analog signals directly to analog pins then there’s no need for the whole comparator setup on this board (we’re talking about AYAB-esp32 here). Personally I’ve been wondering why the comparators were there, as it seemed simpler to route the analog signals to ESP32 pins (via a voltage divider to keep them under 3.3v), but I assumed they were there for a reason.

If they don’t need to exist, then I agree it would be best to keep the wiring similar to what we should have on the upcoming fixed Arduino shield: left (and right on non-910) analog signals going to analog pins, and 910 digital signals going to digital pins.

jpcornil-git, 2025-01-04:
Agree, this is what I would do as well, i.e. no comparators but direct connections (GPIO configured as analog input or digital inputs with pullup enabled for KH930/KH910 EOL_R respectively) for existing shield and esp32 (passive level shifters for the latter to scale analog signal from 5V0 down to 3V3).

I believe comparators are there to offer:
- a full digital interface and ease interfacing with upcoming 3V3 MCU (easy to address)
- no differences between KH910 and KH930 from a FW perspective (not true anymore)

Given that they aren't must-have and they break current EOL implementation, I would revert to the shield approach.

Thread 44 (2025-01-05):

ayab-shield, fix ground pour and silkscreen/assembly layers, EOL R circuitry

VIPQualityPost, 2025-01-05:
The import was brought over and fixed up, need to patch EOL R and small quality of life things.

Closed 2025-04-14.

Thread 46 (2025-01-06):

ayab-shield: Make the top pour GND instead of +5V

vthunder, 2025-01-06:
There’s been at least one instance on someone accidentally bridging IC pins to +5V because the top pour is +5V and the lines are thick and close to the pins. The idea here is to add some space and make the top GND to reduce this likelihood.

@VIPQualityPost  please correct if I’ve misstated anything here

VIPQualityPost, 2025-01-06:
nope, spot on. Do you want to fix it?

Closed 2025-04-01.

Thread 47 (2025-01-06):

ayab-shield:  Add assembly components to BOM

vthunder, 2025-01-06:
The KiCad project for the shield only contains symbols actually placed on the board, but there are a few more required for assembly (eg extension cable, buzzer).

These should be added so they appear on the KiCad BOM.

Maitresinh, 2025-02-19:
Also : i've found the values for the BOM here

https://www.ayab-knitting.com/ayab-shield/

But the link to make the brother connectors (KH1910 or 920) is dead.
Does the components listed in the BOM for the connectors are still the good ones ?

jonathanperret, 2025-02-19:
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

The precise manufacturer and shop references may be obsolete (or not, I don’t actually know) but I can tell you the part requirements for the shield have not changed since that page was written.

>
> Edit : also... ULN2803APG,CN is not avaiable anymore. Digikey propose a substitute (TBD62083APG). Is that ok ?

That part looks superficially similar to the ULN2803 but I wouldn’t try substituting it. ULN2803 is a very common part with multiple manufacturers, that should be easy to find in DIP18 format, just search for that. A quick search on Digikey returns an ST part that is in stock: https://www.digikey.fr/fr/products/detail/stmicroelectronics/ULN2803A/599591 — a bit pricey but you only need 2 of those.

Maitresinh, 2025-02-19:
Thanks.

Regarding how to make the connectors, there is no copy of the dead link on archive.org. If anyone could post it again....

jonathanperret, 2025-02-20:
> Regarding how to make the connectors, there is no copy of the dead link on archive.org. If anyone could post it again....

Sure. The link was broken by #39 which moved the PDF to here: https://github.com/AllYarnsAreBeautiful/ayab-hardware/blob/main/ayab-shield/pdf/kh9xx_power.pdf

You may be disappointed though, this PDF only contains a drawing of the outline of the part you need to make (3D printed or otherwise) to complete the connector.

VIPQualityPost, 2025-04-01:
> You may be disappointed though, this PDF only contains a drawing of the outline of the part you need to make (3D printed or otherwise) to complete the connector.

Should we upload a .step file so that users don't have to draw this (primitive) shape from scratch? I have the part already from when I made a full model of the Brother power connector, I think...

Maitresinh, 2025-04-01:
I've made one.
Here it is : https://cloud.500nuancesdegeek.fr/index.php/s/4n2qd43M9nNtSRH

Closed 2025-04-07.

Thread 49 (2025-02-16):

A bit confused / A few questions

Maitresinh, 2025-02-16:
A few questions before diving into this wonderfull hack (many thanks by the way) :

**1- Which one to choose**
"Ayab interface" := the  take from mad scientifst (using adafruit) based on the first Ayab interface using arduino uno, but with a new form factor
     "Ayab Esp32" = the new design from AYAB, adaptating the mad scientist take with an ESP32 instead of Adafruit

So, Ayab Esp32 should be considered as the latest ayab, using Esp32 for opensource and cost shake.

Am i right ?

**2. BOM**

I've found that
https://github.com/AllYarnsAreBeautiful/ayab-hardware/blob/main/ayab-interface/assembly/ayab_rs_oshw.csv

...but for ayab interface. I suppose the BOM file is into kicad files.

**3.** Installation and soldering

Doc is outdated. I suppose the installation (cables) is the same as for Ayab 1.0

**4. Flashing**

Where is the file/package ? I counted find a "script" folder into the Esp32 ayab folder

Maitresinh, 2025-02-18:
1/ Solved. I used the ESP32 PCB, assuming it's the last one.
2/ Solved. Found the BOM in Kicad

But still wondering with scripts for flashing

jonathanperret, 2025-02-19:
Hi! Sorry for the delay in responding to your questions.

AYAB Interface: you have the nomenclature mostly correct, except that the original (and still updated/manufactured) AYAB hardware is usually called the "AYAB Shield" whereas "AYAB Interface" is reserved for the EMSL remake that includes a microcontroller board (https://wiki.evilmadscientist.com/AYAB_Interface) and has a larger form factor. Those two boards have essentially the same schematic and share the same firmware. As of this writing, the EMSL board is no longer being manufactured by EMSL, and while there are a couple of vendors online that can build and sell them on demand, I believe most new AYAB users currently go for the AYAB shield and an Arduino Uno, probably because it is much easier to DIY.

If you're only interested in building working AYAB hardware, your simplest option would be to get an AYAB shield manufactured from the KiCad project in https://github.com/AllYarnsAreBeautiful/ayab-hardware/tree/main/ayab-shield. It doesn't look like we have an exported BOM file for the shield but the part list is pretty straightforward. Of course you could also just order a kit from https://ko-fi.com/s/716cda7fa9.

If you're interested in building an AYAB Interface specifically, it will be a bit more involved — the fabrication files are in this repository (https://github.com/AllYarnsAreBeautiful/ayab-hardware/tree/main/ayab-interface) but I can't speak to the full validity of the BOM — there's at least one open issue on that: https://github.com/AllYarnsAreBeautiful/ayab-hardware/issues/42.

Regarding AYAB-ESP32 now: this is an entirely new board design that @VIPQualityPost has been working on, based as the name implies on an ESP32 MCU instead of an Atmega328p. You shoud be aware that that design is still in development and has not to the best of my knowledge been used in a knitting machine yet. There's at least [one identified issue](https://github.com/AllYarnsAreBeautiful/ayab-hardware/issues/43) that implies upcoming changes to the design. And no firmware has been written for that board yet.

I've just seen that you've found an older issue about the state of the project (https://github.com/AllYarnsAreBeautiful/ayab-hardware/issues/36#issuecomment-2647007830) so this is probably redundant information at this point.

Maitresinh, 2025-02-19:
thanks for your reply.

In order to sumarize and check if i understand everything:

- **Ayab shield :** the first one with an arduino. Simple and working
- **Ayab interface** : EMSL version. Kicad files are on the Github under /Ayab interface. Working using the same arduino script than Ayab Shiled
- **Ayab ESP32** : the new version in process. PCB are on the Github, but the scripts are not. Still in progress.

Now the questions about the ESP3 version :
- Is the PCB working ? (i understand it has not been tested yet, but i mean, do we have to expect changes ?)
- Is the an even (very) approximative date for the release of the (first) script ?

-

VIPQualityPost, 2025-04-01:
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

I think there are some plans to start working on firmware for this board very soon! There will be some large changes in the firmware to move to a more flexible architecture (ayab-async) so this will require a good bit of work.

As far as the board is working: yes, it works but there are some changes to be made due to later discoveries (#43 ), I will fix them this week and open a PR.

Maitresinh, 2025-04-01:
ok. thanks for your answer. I will wait for the firmware.
Meanwhile, I've made 10 units of this PCB. If anyone wants one, i can send it by the post (i only charge 8 euros + shipping to cover the cost)

Closed 2025-02-19.

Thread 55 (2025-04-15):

Bigger/longer solder pads on shield v1.5

t0mpr1c3, 2025-04-15:
Jonathan and Viktoria raised a point on the Discord about the solder pads on the shield. Version 1.4 has mostly large, elongated pads which are easy for inexperienced users with cheap soldering irons to assemble. Version 1.5 should keep these long solder pads where possible. LEDs and resistors will have smaller pads, but it should be possible to switch from circular pads to those with an elongated or octagonal shape.

VIPQualityPost, 2025-04-17:
Do you want to roll this in on your open PR or do you want me to do it after it gets merged?

t0mpr1c3, 2025-04-20:
Let's do it after the merge. There will probably be other changes too.

Closed 2025-05-12.

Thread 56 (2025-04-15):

Increased clearance around holes in shield v1.5

t0mpr1c3, 2025-04-15:
I think the holes in the shield are potentially useful to secure the shield on top of the arduino, and indeed to attach the whole assembly to another surface, but only if they have sufficient clearance around them for a washer or pan screw head. The limits of this clearance should be allocated using the courtyard feature.

VIPQualityPost, 2025-04-17:
I don't particularly think they are useful and don't see a way to increase clearance - the board is already too packed with the through-hole parts used. I would rather see them go away but I think opinion on this may be mixed.

t0mpr1c3, 2025-04-20:
I like them but only if there is sufficient clearance. I'm not sure what you can do with a 3mm hole that has 3.2mm of clearance, so getting rid of the holes could be the consensus option.

t0mpr1c3, 2025-05-05:
Close as won't fix.

Closed 2025-05-05.

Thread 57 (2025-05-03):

LED resistor values on shield v1.5

t0mpr1c3, 2025-05-03:
Currently the values of the resistors in series with the LEDs on v1.5 of the shield are 150 ohms. This seems right for an LED with a 2V drop on a 5V line since (5-2)/150 = 0.02 or 20 mA. Red and yellow LEDs typically do have a 2V drop, but green LEDs typically have a 3V drop so 100 ohms might be more suitable for that one.

t0mpr1c3, 2025-05-05:
Another issue here is that the pins on the Uno R4 can only source 8mA of current, whereas the R3 could provide 20 mA. So the values of 100 & 150 ohms should be increased to 270 & 390 ohms in that instance.

jonathanperret, 2025-05-05:
The current limitation on R4 pins is a very good point. Sticking to a single target current however isn't the whole story, as different LEDs have a different brightness/current relationship. You can find LEDs that will shine brighter at 5mA than others at 20mA, even within the same color. See https://news.sparkfun.com/5461 for example for one way a device manufacturer approached it.

I think that leaves us with a few options:
1. pick a single target current (e.g. 8mA, probably lower for a safety margin on R4) and pick resistors based on the actual forward voltage of the selected LEDs;
2. pick a single resistor value — like the current design, but higher to make sure the R4's pin current limit isn't exceeded — and try to select LEDs that have a relatively similar brightness at that current;
3. do a bunch of testing of various LED models to select the best set of resistor values for (approximately, as that will depend on the human observer in any case) consistent brightness and write down the selected resistor values and LEDs to the BOM.

I would favor option 2 for the through-hole shield, as ease of assembly is an important factor in that case and minimizing the BOM length helps with that. So, bumping the resistors from 150 Ω to 560 Ω would be enough I guess?

For SMT, professionally assembled boards, the equation is different and I suppose one could do the research that goes with option 3. Not sure that's worth the effort though, maybe option 1 would be enough.

t0mpr1c3, 2025-05-05:
You are right that the brightness, and hence the resistor values, depends on the particular LEDs that are specified.

Typically LED brightness (in mcd) is specified at 20mA but if you dig into the datasheets you can usually find the brightness/current curve. It's generally more or less linear up to 20 mA.

The voltage drop also varies with the current applied. These curves are also in the datasheet.

So if you go by the ratings in mcd you can specify the brightness that you want and calculate the current and forward voltage and get the value of resistor that is required.

It doesn't require all that much experimentation, it's more about choosing suitable LEDs and working backwards from there.

So probably we need to consider whether the LEDs specified in the BOM are suitable (i.e. brightness enough at lower current).

t0mpr1c3, 2025-05-05:
@VIPQualityPost The LEDs that are specified currently, according to the schematic anyway, are HLMP-1640-B00A1 for the green LED, which is diffuse, and HLMP-NG07 for the red and yellow LEDs, which are water clear. Is that up to date? IMO they should all have a diffuse lens.

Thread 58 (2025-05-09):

3 pin connectors in v1.5 have wrong pinout

t0mpr1c3, 2025-05-09:
Comparing the schematic for v1.5 to that of the EMSL interface (https://github.com/AllYarnsAreBeautiful/ayab-hardware/blob/main/ayab-interface/schematic/ayab_rs.pdf):

v1.5 JP7 is equivalent to EMSL J6B.
EMSL J6B has pinout 1=+5V, 2=GND, 3=EOL_R
v1.5 JP7 has pinout 1=GND, 2=EOL_R, 3=+5V (wrong)

v1.5 JP7A is equivalent to EMSL J6C.
EMSL J6C has pinout 1=EOL_R, 2=GND, 3=+5V
v1.5 JP7A has pinout 1=GND, 2=EOL_R, 3=+5V (wrong)

v1.5 JP2 is equivalent to EMSL J7A/J2B.
EMSL J7A/J2B have pinout 1=+5V, 2=GND, 3=EOL_L
v1.5 JP2 has pinout 1=EOL_L, 2=GND, 3=+5V (wrong)

v1.5 JP2A is equivalent to EMSL J2C.
EMSL J2C has pinout 1=EOL_L, 2=GND, 3=+5V
v1.5 JP2A has pinout 1=EOL_L, 2=GND, 3=+5V (correct)

jonathanperret, 2025-05-10:
Ooh, good catch!
Here's a comparison with the 1.4 schematic and the Interface schematic:

| 1.4 | 1.5 | Interface |
|-|-|-|
|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|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|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|
|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|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|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|

Obviously the JP7/JP7A footprints are wrong in 1.5, although since they are only ever used with an extension cable, the pin order could in theory be fixed in the cable. By the way, as Victoria mentioned on Discord, footprint JP7A shouldn't even exist, it's never used to fit a connector on the board.

JP2 on the 910 is the one that uses a cable, so likewise having it flipped is not a huge problem. But it is a problem for the 930.

It is interesting to note that Brother flipped the 2mm-pitch connectors on the KH965/KH900, except for those going to the solenoids.

Once the pin order for JP7 and JP2 is fixed, some thought could be given to connector orientation. In the 1.4 shield, the 2mm-pitch connectors are in two different orientations, which makes assembly more error-prone:

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

The Interface on the other hand has all the connectors facing the same side, which is nice:

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

t0mpr1c3, 2025-05-11:
Yes, this is a nice feature of the EMSL shield. It would be nice to have the chips orientated the same way too.

I'm not sure whether there would space to do it on the through hole shield without going to a 4 layer PCB. It's worth thinking about, but perhaps it might be considered a feature rather than a fix and could be postponed for v1.5.

t0mpr1c3, 2025-05-11:
If I understand Viktoria right, she is saying that neither JP7 nor JP7A ever need to be populated so we only need one set of 3 holes to solder the ribbon cable into. I guess that is true, unless you wanted a shield that worked for both KH965 and KH900 machines, in which case you might want to solder 2 cables, one for each type of connector.

t0mpr1c3, 2025-05-11:
If we could get rid of JP7A, I wonder if there would be room to lay the resistors down flat. I just don't like them sticking up unless they are covered in heat shrink.

jonathanperret, 2025-05-11:
> Yes, this is a nice feature of the EMSL shield. It should be possible -- have a look at [`smd`/arduino_shield_smd/arduino_shield_smd.kicad_pcb](https://github.com/AllYarnsAreBeautiful/ayab-hardware/blob/smd/arduino_shield_smd/arduino_shield_smd.kicad_pcb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)

Not sure what I was meant to look at in that project but it is indeed very easy to flip the connector, just did a quick and dirty test and there's plenty of room to route the traces the other way:

|before|after|
|-|-|
|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|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|

jonathanperret, 2025-05-11:
> If I understand Viktoria right, she is saying that neither JP7 nor JP7A ever need to be populated so we only need one set of 3 holes to solder the ribbon cable into. I guess that is true, unless you wanted a shield that worked for both KH965 and KH900 machines, in which case you might want to solder 2 cables, one for each type of connector.

Yes, JP7 is only ever used to solder wires. Here are pictures of the three variants with connectors populated, from the soldering instructions document:

|machine|shield|
|-|-|
|KH910/KH950|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|
|KH930/KH940|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|
|KH900/KH965|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|

As you can see JP7/JP7A aren't ever populated with a connector. On the 910/950 they stay unused (those signals are in the 10-pin JP5) and on other machines an extension cable goes there.

If you wanted a shield that can be moved between a 930/940 and a 900/965 (by the way, careful with the nomenclature here, the KH900 is an actual model, one of the last to come out and it uses the same 2mm connectors as the 965) I guess you would populate both sets of connectors and solder two cables into JP7? Even if you put two sets of holes there for that case, there is no reason for one of the footprints to be 2mm-pitched. And maybe it would be smarter to solder just one cable to the board and have it split at the other end. Quite a niche scenario in any case IMHO.

jonathanperret, 2025-05-11:
> If we could get rid of JP7A, I wonder if there would be room to lay the resistors down flat. Either that or put heat shrink in the BOM. I just don't like them sticking up unless they are covered in heat shrink. The resistors are vulnerable to getting knocked over and the unprotected leads can cause shorts.

If we need more space on the board, I guess there's always the buzzer connector that can go — I heard Viktoria stopped packaging buzzers with her kits anyway, probably because user feedback was unanimous that the sounds from the app in 1.0 were so much better than the awful bleating from that electromechanical alarm buzzer.

I would have liked to avoid creep in these updates though… really the only critical thing that motivated an update to the (through-hole) shield was the right-side sensor fix for the 910, and then there's the move from Eagle to KiCad. But that kind of creates a context in which it's tempting to slip in every change we can think of, even though each of those needs to be tested, documented, and so on which can snowball into getting stuck with lots of unproven changes (to wit: this issue) and the project in a state of not being able to produce working hardware.

In my mind we could have just changed that couple traces required for the right-side fix, and we wouldn't even have had to redo all the pictures in the soldering instructions documents. But I also appreciate that stuff is being improved, I just hope we can soon get to a stable state again.

t0mpr1c3, 2025-05-11:
I am sensitive to that. IMO the change to Kicad was always going to mean
redoing the pictures. It can wait but FWIW don't think laying the resistors
flat would require documenting or testing.

On Sun, May 11, 2025, 07:01 Jonathan Perret ***@***.***>
wrote:

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

jonathanperret, 2025-05-11:
> I am sensitive to that. IMO the change to Kicad was always going to mean
> redoing the pictures. It can wait but FWIW don't think laying the resistors
> flat would require documenting or testing.

I can agree that it would not require _more_ documentation or testing than what we're in for anyway with the changes already done, so I'd be fine with tweaking the resistor footprints if there is space on the board — not that I'm in a position to decide for or against anyway.

jonathanperret, 2025-05-12:
Here's another point I just thought of regarding connector orientation: it would be good to keep the ability to use angled connectors on the edge of the board, I think Victoria uses those for the 965.

Looking at the current shield on `main`, it would be a problem:

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

Based on the shield pictures above, it seems the angled versions of the connectors have their "cut corners" on the bottom. With the solenoid connectors as they are now, they would face towards the inside of the shield.

jonathanperret, 2025-05-12:
> That's a fair point. But to be completely honest, I don't trust the pictures in the soldering document. Either the "1" is at the wrong end on the v1.4 silkscreen, or the connectors on the left hand side of the board are back to front.

OK, ignoring that photo, here's a [Molex datasheet](https://www.mouser.com/catalog/645/usd/1640.pdf):

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

Regardless of pin 1's position, these drawings clearly show that the angled version of the header has the corner cutouts on the bottom. So, with the way the connectors are set up on the 1.5 shield currently:

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

substituting an angled header will not work. And given that these are obsolete parts I think it's not a bad idea to keep options like that open.

In fact now that I think about it, you're probably right that the problem is the `1` on the 1.4 silkscreen. Indeed, comparing the 1.4 schematic to the Interface schematic one can see that the pin numbers are reversed on the shield. There's even a note on the Interface schematic about this!

| 1.4 shield | 1.5 shield | Interface |
|-|-|-|
|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|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|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|

I guess the connector pinout wasn't looked at closely on the shield as it was always easy to orient the connector whichever way worked — and the initial versions used only unpolarized headers. And I imagine it's a coincidence that the correct orientation worked out for angled headers, but as I said above I think that's a useful property to keep.

t0mpr1c3, 2025-05-12:
OK, that makes sense. Is the orientation of the right angle KH930-style connectors also this way round? That is to say, with pin 1 on the right hand side when the wires are pointing down.

t0mpr1c3, 2025-05-12:
Never mind, I just had a look at the Molex 5267 series and I can't find any right angle connectors.

jonathanperret, 2025-05-12:
> Never mind, I just had a look at the Molex 5267 series and I can't find any right angle connectors.

Oh they exist, they just have a different series number. I think it is 5268 in that case. Yep, looking at the datasheet for the plug you can see both 5267 and 5268 are the mating parts: https://www.molex.com/en-us/products/part-detail/50375083.

To answer your question, yes it looks like they are numbered the same:

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

 Pin 1 is on the left side looking into the connector when the cut corners are on the bottom (which coincides with the wires pointing down, in the case of an angled connector).

ETIBerlin, 2025-05-12:
Concerning straight or angled 8 or 10 pin connectors, the angle saves bending the cable from the machine by 90 degrees, but in practices there is no difference if straight or bent. It doesnt really affect how much space it takes up or how it fits into the machine....therefore imo negligable.
When looking at how the shield is fitted into the machine (the connectors facing upwards) then the previous orientation in 1.4 of the connectors is best, as you dont have to twist the cables to fit it to the board. Since the interface fits in the machine like the original board (connectors facing down) it makes sense they have the same orientation as the original hardware which is opposite to shield 1.4.

jonathanperret, 2025-05-13:
> When looking at how the shield is fitted into the machine (the connectors facing upwards) then the previous orientation in 1.4 of the connectors is best, as you dont have to twist the cables to fit it to the board. Since the interface fits in the machine like the original board (connectors facing down) it makes sense they have the same orientation as the original hardware which is opposite to shield 1.4.

Interesting! Some people do put the shield the other way though? See https://www.thingiverse.com/thing:3281342/files for example.

Closed 2025-05-13.

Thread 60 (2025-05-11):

2mm pitch 5 pin connector has wrong pinout in v1.5

t0mpr1c3, 2025-05-11:
It's back to front.

From EMSL interface schematic:

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

From v1.5 schematic:

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

jonathanperret, 2025-05-11:
I guess it was already the case in the 1.4 shield, but without a pin 1 mark on that 2mm footprint, one just had to know the connector needed to be flipped, as documented in the soldering instructions:

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

Like discussed on #58, having a consistent connector orientation would sure be better.

t0mpr1c3, 2025-05-11:
Yes, the error in the schematic can be resolved by flipping the connector.

Closed 2025-05-13.

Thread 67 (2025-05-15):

Options for I2C header

t0mpr1c3, 2025-05-15:
Background:
Currently both the shield and the EMSL interface use 2.54mm pin header with a 5V-SDA-SCL-GND pinout. The ESP prototype uses a 1mm pitch JST SH connector with GND-3.3V-SDA-SCL pinout, that is identical to the Sparkfun QWIIC specification. This pinout is the closest thing that exists to a standard, and has been also adopted by Adafruit Stemma, which uses 2mm pitch JST PH connectors, and Seeed Studio's Grove, which uses proprietary connectors with 2mm pitch. QWIIC uses only 3.3V, whereas both Stemma and Grove allow 5V lines and signals.

Problem:
The 2.54mm pitch header on the shield and interface has the advantage of being generic and robust. The downsides are:
* The connector is somewhat bulky for something that carries low voltage, low current signals.
* The arbitrary pinout requires documentation, preferably on the PCB itself, not least because...
* ...the header is non-polarised, which means that it is possible to accidentally plug in a matching socket back to front.
These are all good reasons to adopt one of the more standard Qwiic/Stemma/Grove connectors instead.

The ESP prototype has opted for a Qwiic-compatible header, which is perfectly reasonable given that the ESP32 is powered by 3.3V. However, this makes it somewhat unsuitable for the shield and interface, which employ 5V microprocessors which would require level shifting to output 3.3V signals. In addition, the 1mm pitch hardware used by Qwiic is fiddly and less than robust for an external connection.

Suggested solution:
Ideally we would standardise on a single connector that could be used by all the AYAB hardware. Neither the pin header used by the shield nor the Qwiic connector chosen for the ESP prototype seems to fit the bill. Of the alternatives, both 2mm pitch connectors, Stemma is preferable to Grove because it uses generic connectors that are cheap and universally available.

t0mpr1c3, 2025-05-16:
A slight correction to the above: while it is true that there has always been a through hole version of the shield -- and there is a strong consensus that there should continue to be one -- there have in the past been versions of the shield that have incorporated SMD components, e.g. v1.2 https://github.com/AllYarnsAreBeautiful/ayab-hardware/blob/6542afcab6f2a81585d12e9e20f1e5dc20c1d853/Shieldv1x/10_ayab-arduino/smd/export/arduino_shield.pdf

jonathanperret, 2025-05-16:
Thanks for the recap @t0mpr1c3 .

Regarding the choice of connector for the ESP32 board, if I remember correctly the consensus reached at the last meeting, we agreed to keep the ESP32 for networking only and essentially mirror the Arduino+shield hardware on the board.

With that in mind I think it would make sense to have a 5V I2C connector on the ESP32 board, connected to the 5V MCU used for low-level I/O. And of course we would use the same connector as on the shield — I favor Stemma as well (JST PH 2mm).

That connector would probably be used for an automatic color changer once sufficient energy is gathered to bring that project to fruition.

Note that this would not preclude having an additional Qwiic (3.3V, 1mm) connector directly connected to the ESP32, to connect a display module for example.

t0mpr1c3, 2025-05-26:
By the way the EMSL interface with Metro Mini v2 has a Stemma QT I2C connector built in, as well as the pin header

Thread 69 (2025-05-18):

Allow Hirose connectors on v1.5

t0mpr1c3, 2025-05-18:
The intention is that vertical pin headers, right angle pin headers, and verrtical Hirose connectors should all be options for the KH910 solenoid connectors in v1.5. The footprints used currently are those for vertical pin headers. Hirose connectors are wider and changing to Hirose footprints would allow sufficient lateral space to fit them on the PCB. However, it is also necessary to space the connectors in this lateral dimension so that they would not obstruct each other if right angle connectors were used. To achieve this without making the shield wider, it will be necessary to eliminate the mounting holes and allow the lateral flanges of the Hirose socket to extend further than the physical outline of the PCB, that is, to have them hang over the sides of the board.

Closed 2025-07-06.

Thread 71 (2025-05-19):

Fix orientation of knitting machine connectors in v1.5

t0mpr1c3, 2025-05-19:
The pinouts of the solenoid headers (8 and 10 pin headers that connect to the knitting machine, other than JP5) are reversed pinout on the v1.5 schematic compared to the EMSL interface schematic.

Their orientation also needs to change on the PCB to accommodate right angle headers.

The orientation of some of the other knitting machine connectors can be changed so that they are all turned the same way (that is, with pin 1 towards the the same side of the board) to ease assembly.

Closed 2025-07-06.

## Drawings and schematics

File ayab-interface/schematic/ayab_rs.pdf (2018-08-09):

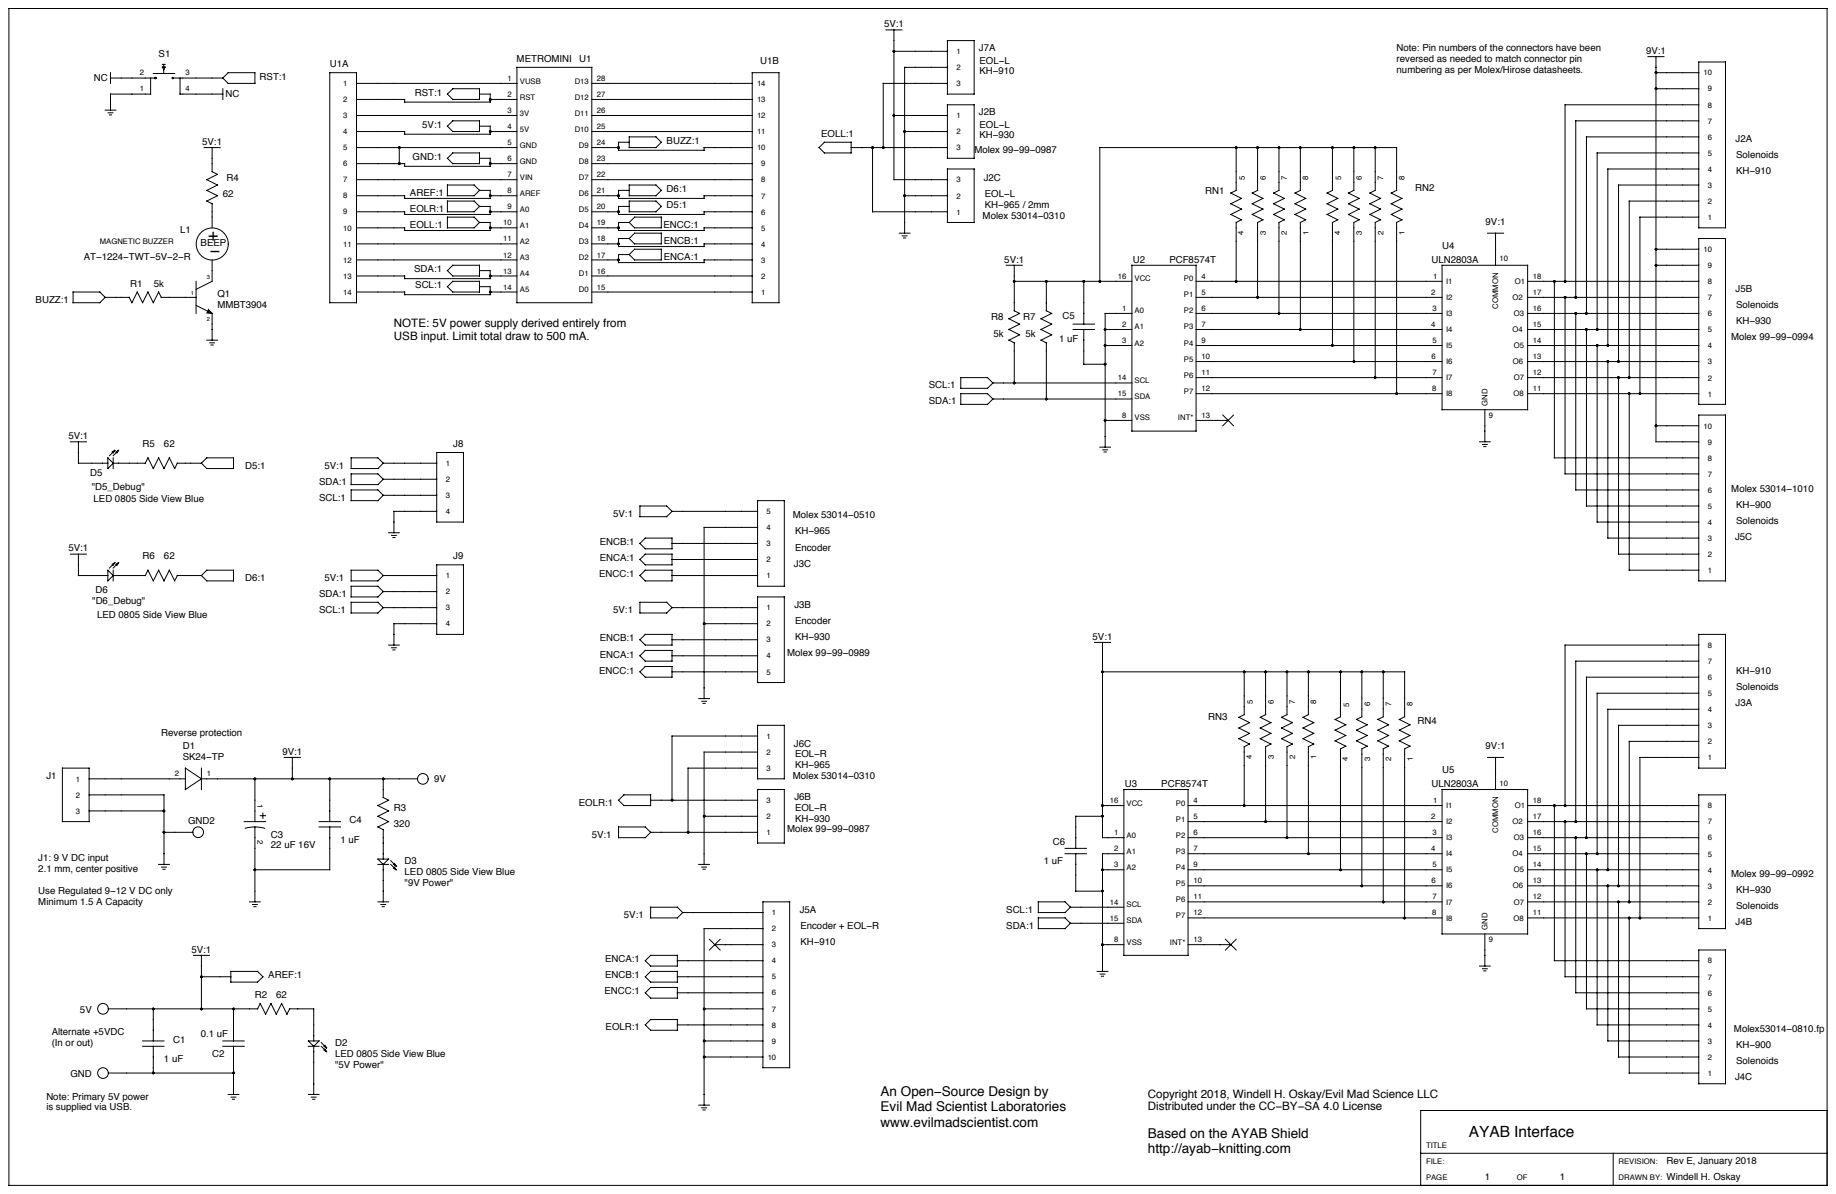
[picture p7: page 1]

Note: Pin numbers of the connectors have been
reversed as needed to match connector pin
numbering as per Molex/Hirose datasheets.

NOTE: 5V power supply derived entirely from
USB input. Limit total draw to 500 mA.

Use Regulated 9−12 V DC only
Minimum 1.5 A Capacity

An Open−Source Design by
Evil Mad Scientist Laboratories

Note: Primary 5V power
is supplied via USB.

Copyright 2018, Windell H. Oskay/Evil Mad Science LLC
Distributed under the CC−BY−SA 4.0 License

http://ayab−knitting.com

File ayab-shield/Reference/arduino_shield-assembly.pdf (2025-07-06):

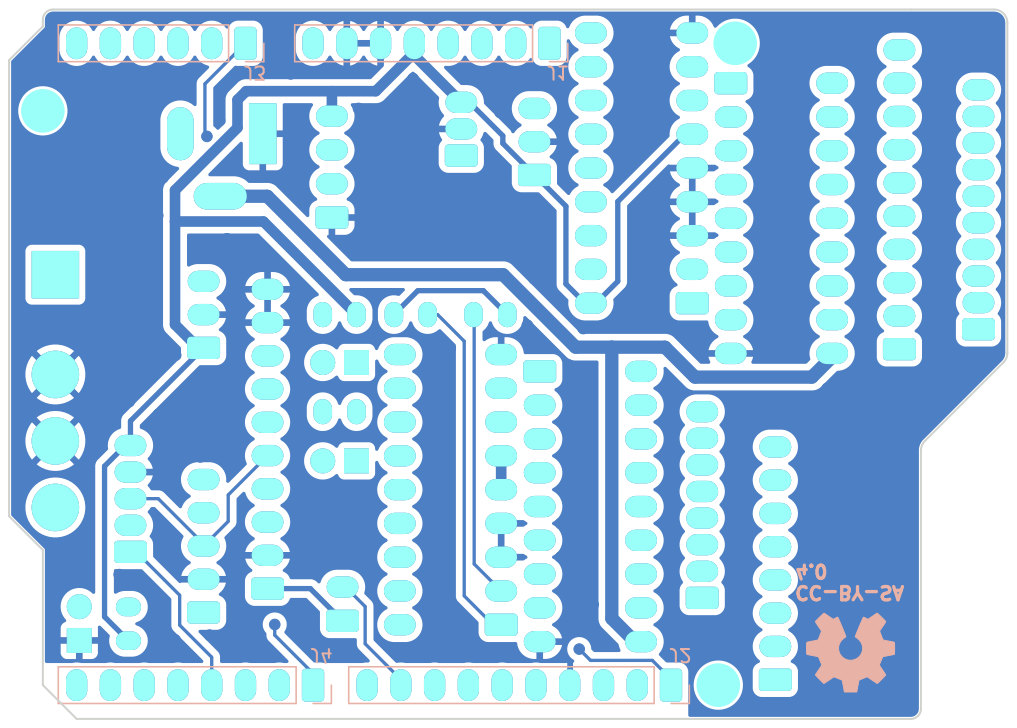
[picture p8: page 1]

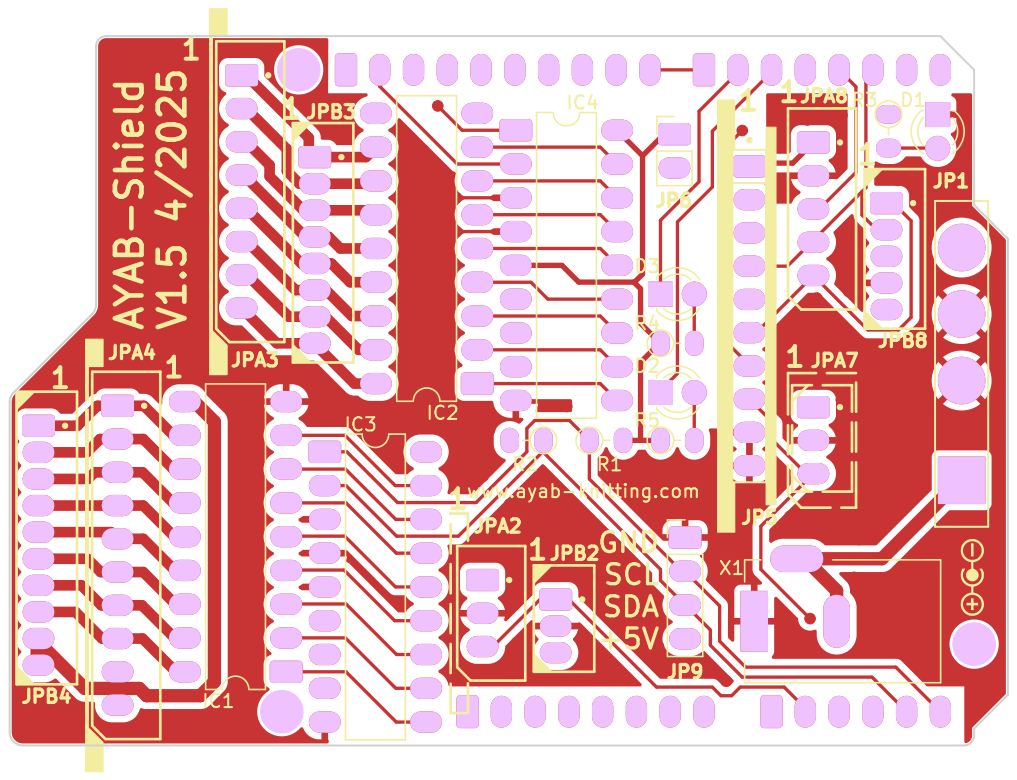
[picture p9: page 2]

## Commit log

2013-09-17 Eagle Schematic erstellt, Knitic Schematics zum Repo hinzugefügt
    [shield_arduino_mega.sch]
2013-09-18 Schematic grundsätzlich erstellt, alles drin bis auf: Buzzer Verdrahtung EOLs und Encoder Entscheidung MEGA oder UNO wg. Interrupts
    [arduino_shield.sch, shield_arduino_mega.sch]
2013-09-18 Added Board Layout File
    [arduino_shield.brd]
2013-09-23 Wired EOLs and ENCODER to Arduino, added Buzzer and Supplyvoltage Jumper
    [arduino_shield.sch]
2013-10-27 Schematic an tatsaechliche Steckerbelegungen angepasst
    [arduino_shield.sch]
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2013-10-29 Pinheader auf 2.5, Summer gändert, Beschriftung
    [arduino_shield.brd, arduino_shield.sch]
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2014-01-21 changed folder structure for new hardware version
    [arduino_Uno_Rev3-02-TH.brd, arduino_Uno_Rev3-02-TH.sch, arduino_shield.brd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]
2014-01-23 initial commit for kicad project
    [arduino_shield.brd, arduino_shield.sch, arduino_uno_r3_compatible.brd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]
2014-01-27 finished connectors for kh-910
    [ayab-apparat-pcb.sch, machine_interface.sch]
2014-02-05 fixed unnecessary merge of ayab-apparat-pcb data to master
    [arduino_uno_r3_compatible.brd, arduino_uno_r3_compatible.sch, ayab-apparat-pcb.sch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]
2014-02-25 started work on improving shield, added reset button to schematic
    [arduino_shield.brd, arduino_shield.sch]
2014-02-25 added kh-930 specific connectors
    [arduino_shield.brd, arduino_shield.sch]
2014-03-02 Finished Board Layout for v1.1
    [arduino_shield.brd]
2014-03-04 added gerber data for ayab-shield-v1.1 added kh-930 manual
    [arduino_shield.brd, arduino_shield.sch]
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2014-04-12 added defines for KH930 fixed pinning for S3 of KH930
    [arduino_shield.brd, arduino_shield.sch]
2014-05-16 Fixed Shield Layout (position of connectors)
    [arduino_shield.brd]
2014-07-16 Resolved issues 8,9,10
    [arduino_shield.brd]
2015-10-14 Created a shield version without SMD-Parts
    [arduino_shield.brd, arduino_shield.sch]
2015-10-16 Finalization of AYAB Shield 1.3 Through Hole
    [arduino_shield.brd, arduino_shield.sch]
2015-11-16 moved through hole pcb to separate directory
    [arduino_shield.brd, arduino_shield.sch]
2015-11-16 moved schematics of SMD version to separate folder
    [arduino_shield.brd, arduino_shield.sch]
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2016-04-17 /andz added 2mm holes for other machine types
    [arduino_shield.brd, arduino_shield.sch]
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2016-11-26 Move all existing files into Shieldv1x directory
    [arduino_Uno_Rev3-02-TH.brd, arduino_Uno_Rev3-02-TH.sch, arduino_shield.brd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]
2016-11-26 Begin adding AYAB-EMS hardware
    [ayab_rs.DrillDrawing.gbr, ayab_rs.VSCORE.gbr, ayab_rs.bottom.gbr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]
2016-11-26 Add schematic, symbols, and PDF
    [ayab_rs.sch]
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2018-05-30 Revision E of Ayab Interface board
    [ayab_rs.sch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]
2019-08-09 Fixed PCF8574ADWR package errata in BOM for Shieldv2x
    [ayab_rs_oshw.csv]
2019-11-22 updated BOM with Mouser part numbers
    [ayab_rs_oshw.csv]
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2019-11-23 further updates to BOM -- alternate part numbers
    [ayab_rs_oshw.csv]
2019-11-23 further updates to BOM -- alternate part numbers (final)
    [ayab_rs_oshw.csv]
2021-01-27 Add missing symbols for AYAB Interface board (gEDA) (#9)
    * Add missing symbols for AYAB Interface board (gEDA)
    * Add missing footprints
    * Additional missing footprints
2021-08-08 Forthcoming version changes to Shieldv2 (#12)
    * remove unused symbols
    * minor version changes to PCB layout
    * document changes in Sheild v2 PCB
    * add .gitignore file
    * substitute Tantalum cap for SMD electrolytic
    * removed unused footprints
    * add logos to PCB
    * update BOM
    * update gerbers
    * OSHW logo in solder mask
    * update gerbers
    * fixed soldermask
    * soldermask on WL logo
    [ayab_rs.sch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]
2021-09-16 PCB version F, final (#14)
    * repaired outline, removed two holes that may have been used during manufacturing but no longer serve that purpose
    * removed two circles from bottom silk
    * add gafrc, ayab_rs.prj files
    * update XY file
    [ayab_rs.sch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]
2024-02-26 ESP32 hardware (#21)
    * start on new ESP32 design
    * first draft schematic
    * add capacitor on solenoid drivers
    * update schematic pdf
    * add spi_sck line
    * fix some comments from jpcornil-git
    * update gitignore
    * add pch MOSFET for polarity protection
    * update zener current limit resistor
    * add ideal diode, remove extra uln2003a, add comparator for analog EOL sensors
    * fix comparator
    * fix folder structure and update gitignore
    * fix pdf and footprint lib
    * comparator biasing and cleanup
    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
    [CP_Elec_8x10.5.step, C_0402_1005Metric.step, C_0603_1608Metric.step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]
2024-02-26 add component selection, bom
    [aux-connectors.kicad_sch, ayab-esp32.kicad_pcb, ayab-esp32.kicad_sch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]
2024-02-26 review ZVD P-ch MOSFET and resistors
    [aux-connectors.kicad_sch, ayab-esp32.kicad_sch, brother-connectors.kicad_sch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]
2024-02-26 first draft layout DRC clean
    [53014-0510.stp, 53014-0810.stp, 53014-1010.stp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]
2024-02-26 update pdf and remove some temp files
    [ayab-esp32-edge.kicad_pcb]
2024-02-26 fix missing silk and remove temp files
    [ayab-esp32.kicad_pcb]
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2024-02-26 archive models, finish layout and prod files
    [53014-0510.stp, 53014-0810.stp, 53014-1010.stp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]
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2024-02-26 Correct footprint and regenerate documentation
    [ayab-esp32.kicad_pcb, ayab-esp32.kicad_sch, ioconditioning.kicad_sch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]
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2024-07-15 Add kicad version of shield design, imported from the eagle source. Also add gerber and drill exports for fabrication.
    [arduino_shield-B_Cu.gbr, arduino_shield-B_Mask.gbr, arduino_shield-B_Paste.gbr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]
2024-07-16 re-do import, this time saving the schematic
    [arduino_shield.kicad_pcb, arduino_shield.kicad_sch]
2024-08-13 Update Kicad import from Eagle with a schematic and general cleanup. Now features: * A linked schematic matching the Eagle one except cosmetic or Kicad specific requirements (e.g., power flags). * Re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
    [arduino_shield.kicad_pcb, arduino_shield.kicad_sch]
2024-08-13 Update gerber exports with latest 1.4TH Rev A Kicad design
    [arduino_shield-B_Cu.gbr, arduino_shield-B_Mask.gbr, arduino_shield-B_Paste.gbr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]
2024-08-13 Update revision in PCB silkscreen and regenerate gerbers
    [arduino_shield-B_Cu.gbr, arduino_shield-B_Mask.gbr, arduino_shield-B_Paste.gbr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]
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2025-01-03 Remove other versions, leave only KiCad through hole shield, simplify folder structure Minor cleanup for latest KiCad version Add part numbers to symbols
    [arduino_Uno_Rev3-02-TH.brd, arduino_Uno_Rev3-02-TH.sch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]
2025-01-03 Actually include changes to sheet meant for last commit, oops
    [arduino_shield.kicad_sch]
2025-02-10 Fix #47, #46, #45, #44
    [arduino_shield.kicad_pcb, arduino_shield.kicad_sch]
2025-03-31 revert design back to old style, but with kicad modifications. Also fix 3D models.
    [arduino_shield.kicad_pcb, arduino_shield.kicad_sch]
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2025-03-31 add JobSet for producing output files
    [arduino_shield-B_Cu.gbr, arduino_shield-B_Mask.gbr, arduino_shield-B_Paste.gbr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]
2025-04-01 clean up zone fill, fix footprint type, clean DRC
    [arduino_shield.kicad_pcb]
2025-04-01 update BOM with arduino headers, change barrel jack to KLDX-0202-AC
    [arduino_shield.kicad_pcb, arduino_shield.kicad_sch]
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2025-04-04 review fixes and link symbols/footprints to kicad ayab library
    [arduino_shield.kicad_pcb, arduino_shield.kicad_sch]
2025-04-07 remove cruft from import and jobset files, add back in later PR
    [arduino_shield.kicad_pcb]
2025-04-15 Update ayab_rs_oshw.csv (PCF8574DWR not PCF8574ADWR)
    [ayab_rs_oshw.csv]
2025-04-15 Change CI to use JobSets instead of manually constructing all outputs with kicad-cli
    add workflow dispatch to manually run jobs
    typo
    Workflow name clarity
    missing $ on env var
    Fix a few more typos
    fix filepaths
    typo for shield project name
    remove conditional check for merged documentation build
    typo
    missing $
    another missing $
    add ghostscript dependency, fix readme name and remove old renders
    Fix ghostscript file naming
    add reference path
    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
    [arduino_shield.kicad_pcb]
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2025-05-12 Fixes to 1.5 shield
    - Add 3d structure to Molex 5267 series parts
    - Add 3d structure to Molex 53014 series parts
    - Add dummy Mfg and P/N for JP1
    - Add missing Mfg and P/N information for I2C pullups and change value to 4K7
    - Add second via in bottom left corner
    - Change pin sockets to pin headers on bottom of shield
    - Clean up PCB
    - Clean up schematic
    - Connect JP5.9 and JP5.10 to GND
    - Delete parts from library that refer to local files
    - Fix errors from ERC/DRC
    - Fix Fab layer
    - Fix imported graphics
    - Remove DRC exclusion for overlap between footprints of IC1 and MH2
    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
    [arduino_shield.kicad_pcb, arduino_shield.kicad_sch]
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2025-05-12 Update schematic from PCB
    [arduino_shield.kicad_sch]
2025-05-12 Fix track clearances
    [arduino_shield.kicad_pcb]
2025-05-12 Tweak clearances
    [arduino_shield.kicad_pcb]
2025-05-12 Try to fix mysterious DRC errors in CI
    [arduino_shield.kicad_pcb]
2025-05-12 Replace top copper GND plane exclusion zone over JPA2/JPB2
    [arduino_shield.kicad_pcb]
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2025-05-13 Reverse pinout of JPB8
    [arduino_shield.kicad_pcb, arduino_shield.kicad_sch]
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2025-05-13 Fix pinout of JPA7
    [arduino_shield.kicad_pcb, arduino_shield.kicad_sch]
2025-05-13 Fix pinout of JPA2
    [arduino_shield.kicad_pcb, arduino_shield.kicad_sch]
2025-05-13 Fix DRC error
    [arduino_shield.kicad_pcb]
2025-05-13 Fix bottom silkscreen
    [arduino_shield.kicad_pcb]
2025-05-13 Remove paste from footprints, make all 2mm pitch connectors have 1mm diameter hole
    [arduino_shield.kicad_pcb]
2025-05-13 Remove dot (indicating pin 1) from footprints
    [arduino_shield.kicad_pcb]
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2025-05-17 Change footprints used on PCB to new footprints with '_LongPads' suffix
    [arduino_shield.kicad_pcb]
2025-05-17 Revert footprints without '_LongPads' suffix to previous versions
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2025-05-17 Reverse orientation of solenoid headers and extend PCB by 1mm
    [arduino_shield.kicad_pcb, arduino_shield.kicad_sch]
2025-05-17 Re-orient JPA7, JPA8, and JPB8
    [arduino_shield.kicad_pcb]
2025-05-19 Switch to Hirose connector footprints, extend board 1mm
    [arduino_shield.kicad_pcb, arduino_shield.kicad_sch]
2025-05-20 Change footprint for JPA7
    [arduino_shield.kicad_pcb, arduino_shield.kicad_sch]
2025-05-20 Add ground plane rule zones
    [arduino_shield.kicad_pcb]
